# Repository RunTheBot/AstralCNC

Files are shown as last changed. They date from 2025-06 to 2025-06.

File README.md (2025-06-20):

# AstralCNC

A Replacement board for the Larken **StarCNC** controller. Built around the RPI Pico, this board is designed with safety and flexibility in mind, allowing for easy integration with external stepper drivers and digital inputs.

Powered by the Raspberry Pi Pico and GRBL-HAL.

Made to referbrish a Larken 24/24 router at my school that is over 25 years old.

# Features
- Supports up to 8 external stepper drivers (5v IO, Step/Dir)
- Supports up to 8 external digital inputs (3.3v IO)
- 5v IO can be switched to 3.3v IO
- 3.3v IO can be switched to 5v IO (for external stepper drivers)
- Built-in 12v regulator for powering all components
- Hardware level emergency stop
  - Emergency stop is not relient on software, ensuring that it works even if the software crashes as the stepper drivers put out a good ammount of EMI
- Hardware level reset button
  - Reset after an emergency stop is not relient on software, ensuring that the machine will remain stopped until it is manually reset
- 4 Analog inputs (ADC)
- All IO is PWM capable

# Images
Larken StarCNC
Schematic
PCB

# BOM

| Name | Quantity | Single Unit Price | Total Price | URL/LCSC | FALSE | Vendor (LCSC unless otheriwse indicated) |
|---|---|---|---|---|---|---|
| Electronics | | | | | FALSE | |
| 47pF | 1 | N/A | $0.29 | C105622 | FALSE | |
| 0.1uF | 1 | N/A | | | FALSE | With My other two projects |
| 22uF | 2 | N/A | $0.17 | C59461 | FALSE | |
| 4.7uF | 2 | N/A | $0.15 | C69335 | FALSE | |
| Molex_KK-254_AE-6410-02A_1x02_P2.54mm_Vertical | 1 | N/A | $0.40 | C5447965 | FALSE | |
| Molex_KK-254_AE-6410-10A_1x10_P2.54mm_Vertical | 1 | N/A | $0.39 | C30169 | FALSE | |
| PinHeader_2x04_P2.54mm_Vertical | 1 | N/A | $0.39 | C2829882 | FALSE | |
| PinHeader_1x04_P2.54mm_Vertical | 7 | N/A | $0.42 | C2935910 | FALSE | |
| Molex_KK-254_AE-6410-03A_1x03_P2.54mm_Vertical | 4 | N/A | $0.71 | C29275 | FALSE | |
| 6.8UH | 1 | N/A | $1.18 | C5296375 | FALSE | |
| BC847 | 3 | N/A | $0.46 | C57668 | FALSE | |
| 220k | 1 | N/A | $0.10 | C22961 | FALSE | |
| 41.2k | 1 | N/A | $0.10 | C2930101 | FALSE | |
| 93.1k | 1 | N/A | $0.10 | C2933266 | FALSE | |
| 22k | 1 | N/A | $0.09 | C2907015 | FALSE | |
| 10k | 6 | N/A | | | FALSE | With My other two projects |
| AP63357 | 1 | N/A | $0.52 | C2158014 | FALSE | |
| 74HC244 | 2 | N/A | $0.77 | C5623 | FALSE | |
| RP2350_Stamp | 1 | N/A | $12.05 | https://lectronz.com/products/rp2350-stamp | FALSE | |
| TXS0108EPW | 2 | N/A | $1.12 | C17206 | FALSE | |
| MOLEX 22013037 | 4 | | $0.27 | C22451182 | FALSE | |
| Molex 2759 seris | 12 | | $0.24 | C22451180 | FALSE | |
| PCB - JLC | | | $9.00 | | | |
| LCSC - Shipping and handling | | | $17.16 | | | |
| lectronz | | | $17.79 | | | |
| JLC - Shipping | | | $8.23 | | | |
| | | | | | | |
| | | | | | | |
| | | | | | | |
| | | | | | | |
| | | | | | | |
| | | | | | | |
| | | | | | | |
| | | | | CAD | | |
| | | | $72.10 | USD | | |
| | | | $72.10 | Total - USD | | |

Why is shipping so expensive? 😭

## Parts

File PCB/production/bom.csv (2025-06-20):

Designator | Footprint | Quantity | Value | LCSC Part #
C11 | 0603 | 1 | 47pF
C12 | 0805 | 1 | 0.1uF
C13, C14 | 0603 | 2 | 22uF
C15, C16 | 0603 | 2 | 4.7uF
J11 | Molex_KK-254_AE-6410-02A_1x02_P2.54mm_Vertical | 1 | Conn_01x02
J31 | Molex_KK-254_AE-6410-10A_1x10_P2.54mm_Vertical | 1 | Conn_01x10_Pin
J310 | PinHeader_2x04_P2.54mm_Vertical | 1 | Conn_02x04_Counter_Clockwise
J311, J312, J313, J32, J37, J38, J39 | PinHeader_1x04_P2.54mm_Vertical | 7 | Conn_01x04_Pin
J33, J34, J35, J36 | Molex_KK-254_AE-6410-03A_1x03_P2.54mm_Vertical | 4 | Conn_01x03_Pin
L11 | L_Chilisin_BMRA00050530 | 1 | 6.8UH
Q21, Q22, Q23 | SOT-23 | 3 | BC847
R11 | 0603 | 1 | 220k
R12 | 0603 | 1 | 41.2k
R13 | 1206 | 1 | 93.1k
R14 | 0603 | 1 | 22k
R21, R22, R23, R24, R25, R26 | 0603 | 6 | 10k
U11 | V-DFN3020-13 | 1 | AP63357
U21, U22 | TSSOP-20_4.4x6.5mm_P0.65mm | 2 | 74HC244
U31 | RP2xxx_Stamp_THT | 1 | RP2350_Stamp
U32, U33 | TSSOP-20_4.4x6.5mm_P0.65mm | 2 | TXS0108EPW

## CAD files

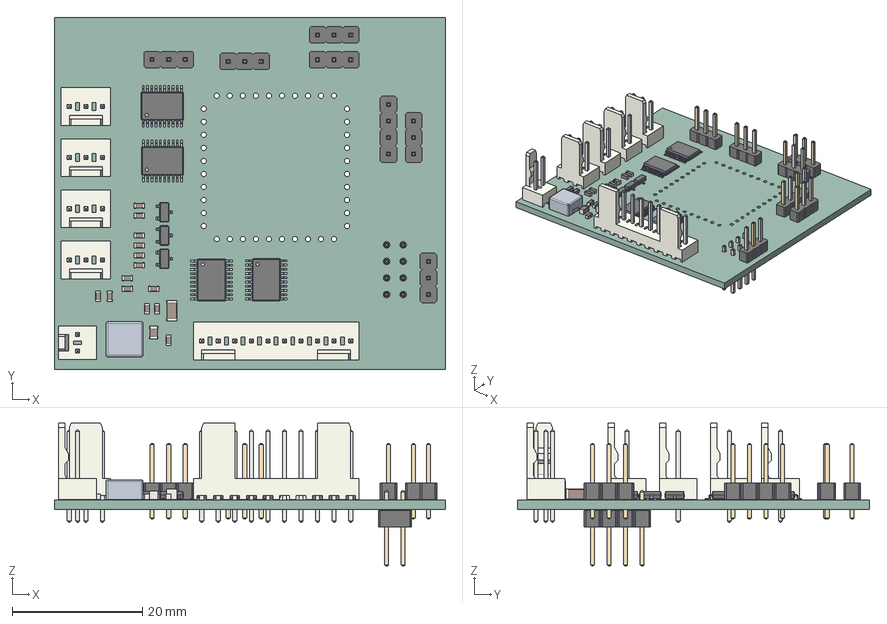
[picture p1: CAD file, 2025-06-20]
PCB/AstralCNC.step
60.0 x 54.0 x 21.9 mm
PinHeader_1x03_P2.54mm_Vertical x 6
C_1206_3216Metric
C_0603_1608Metric x 14
Molex_KK-254_AE-6410-03A_1x03_P2.54mm_Vertical x 4
C_0805_2012Metric
SOT-23 x 3
Molex_KK-254_AE-6410-02A_1x02_P2.54mm_Vertical
TSSOP-20_4.4x6.5mm_P0.65mm x 4
Molex_KK-254_AE-6410-10A_1x10_P2.54mm_Vertical
AstralCNC 1.18.1
PinHeader_1x04_P2.54mm_Vertical
PinHeader_2x04_P2.54mm_Vertical
AstralCNC_PCB

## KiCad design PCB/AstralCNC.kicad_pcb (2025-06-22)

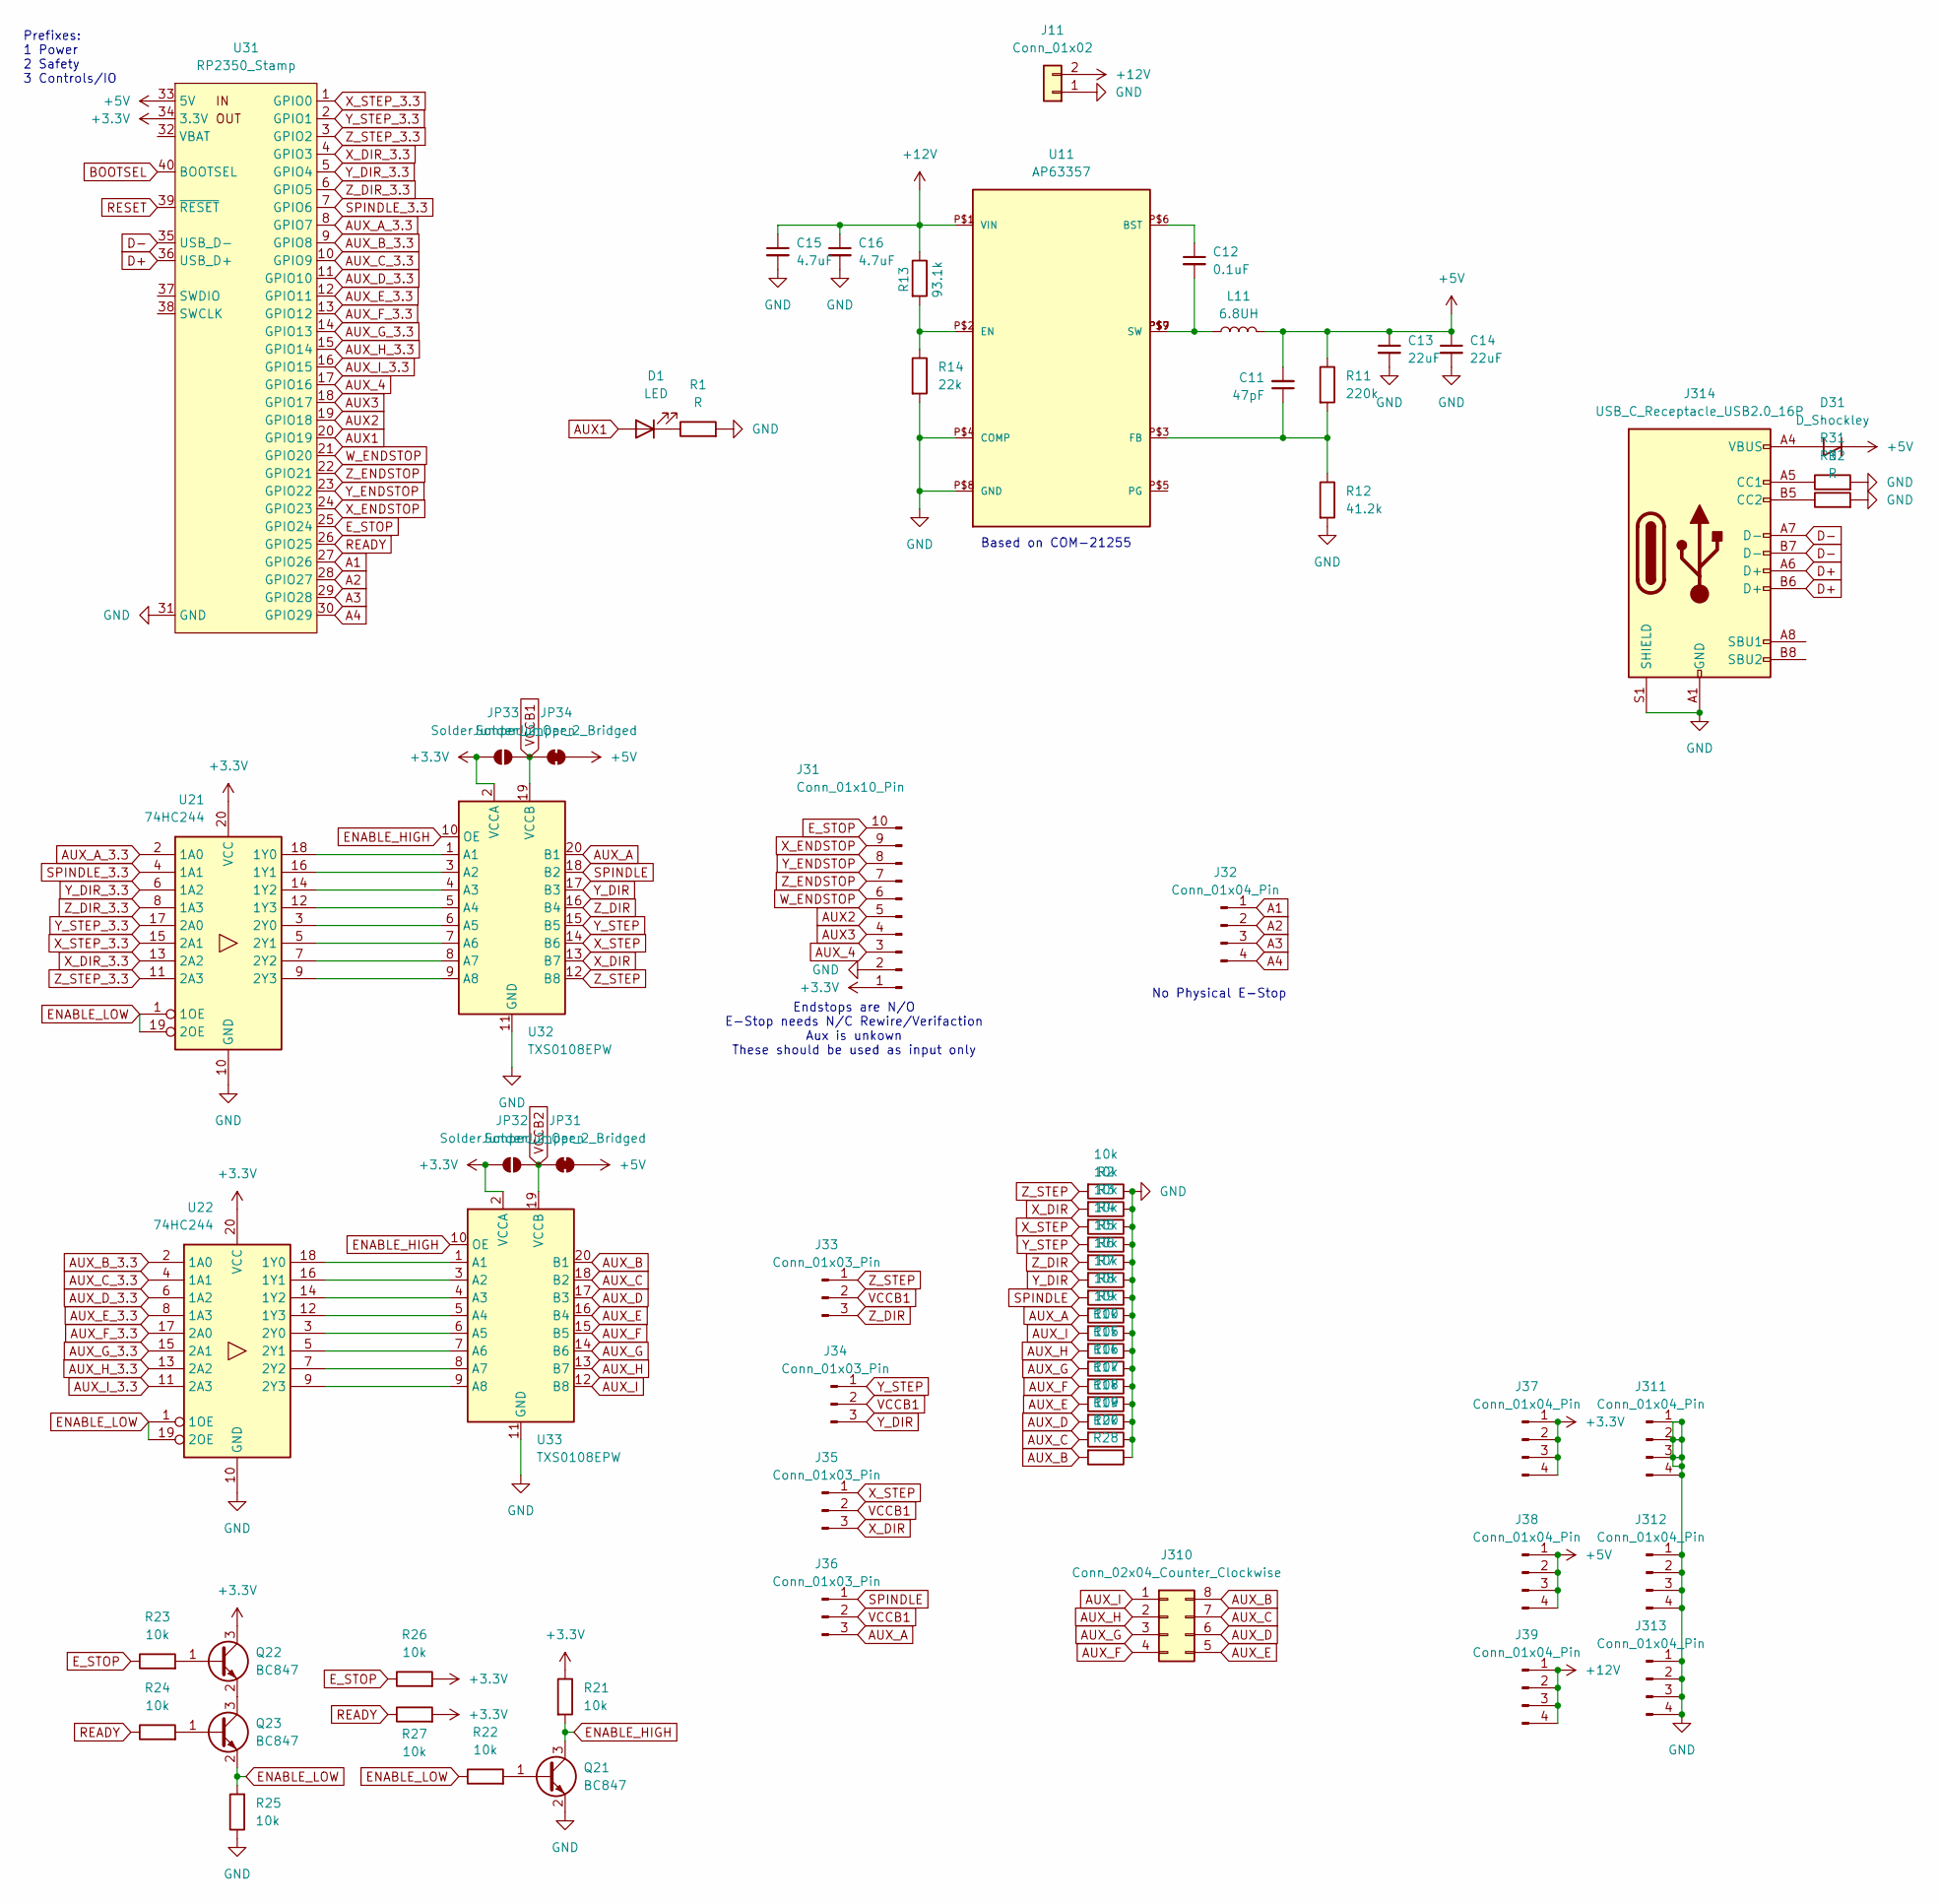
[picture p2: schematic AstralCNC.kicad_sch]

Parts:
C11: 47pF; C_0603_1608Metric_Pad1.08x0.95mm_HandSolder
C12: 0.1uF; C_0805_2012Metric_Pad1.18x1.45mm_HandSolder
C13, C14: 22uF; C_0603_1608Metric_Pad1.08x0.95mm_HandSolder
C15, C16: 4.7uF; C_0603_1608Metric_Pad1.08x0.95mm_HandSolder
D1: LED; PinHeader_1x02_P2.54mm_Vertical
D31: D_Shockley; D_SMA_Handsoldering
J11: Conn_01x02; Molex_KK-254_AE-6410-02A_1x02_P2.54mm_Vertical
J31: Conn_01x10_Pin; Molex_KK-254_AE-6410-10A_1x10_P2.54mm_Vertical
J32, J37, J38, J39, J311, J312, J313: Conn_01x04_Pin; PinHeader_1x04_P2.54mm_Vertical
J33, J34, J35, J36: Conn_01x03_Pin; Molex_KK-254_AE-6410-03A_1x03_P2.54mm_Vertical
J310: Conn_02x04_Counter_Clockwise; PinHeader_2x04_P2.54mm_Vertical
J314: USB_C_Receptacle_USB2.0_16P; USB_C_Receptacle_G-Switch_GT-USB-7010ASV
JP31, JP34: SolderJumper_2_Bridged; SolderJumper-2_P1.3mm_Bridged_RoundedPad1.0x1.5mm
JP32, JP33: SolderJumper_2_Open; SolderJumper-2_P1.3mm_Open_RoundedPad1.0x1.5mm
L11: 6.8UH; L_Chilisin_BMRA00050530
Q21, Q22, Q23: BC847; SOT-23
R1, R31, R32: R; C_0603_1608Metric_Pad1.08x0.95mm_HandSolder
R2, R3, R4, R5, R6, R7, R8, R9, R10, R15, R16, R17, R18, R19, R20, R21, R22, R23, R24, R25, R26, R27, R28: 10k; C_0603_1608Metric_Pad1.08x0.95mm_HandSolder
R11: 220k; C_0603_1608Metric_Pad1.08x0.95mm_HandSolder
R12: 41.2k; C_0603_1608Metric_Pad1.08x0.95mm_HandSolder
R13: 93.1k; C_0603_1608Metric_Pad1.08x0.95mm_HandSolder
R14: 22k; C_0603_1608Metric_Pad1.08x0.95mm_HandSolder
U11: AP63357; V-DFN3020-13
U21, U22: 74HC244; TSSOP-20_4.4x6.5mm_P0.65mm
U31: RP2350_Stamp; RP2xxx_Stamp_THT
U32, U33: TXS0108EPW; TSSOP-20_4.4x6.5mm_P0.65mm

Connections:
+3.3V: J31.1, J37.1, J37.2, J37.3, J37.4, JP32.1 (A), JP33.1 (A), Q22.3 (C), R21.1, R26.2, R27.2, U21.20 (VCC), U22.20 (VCC), U31.34 (3.3V), U32.2 (VCCA), U33.2 (VCCA)
+5V: C11.2, C13.1, C14.1, D31.1 (K), J38.1, J38.2, J38.3, J38.4, JP31.2 (B), JP34.2 (B), L11.2, R11.1, U31.33 (5V)
+12V: C15.1, C16.1, J11.2, J39.1, J39.2, J39.3, J39.4, R13.1, U11.P$1 (VIN)
A1: J32.1, U31.27 (GPIO26)
A2: J32.2, U31.28 (GPIO27)
A3: J32.3, U31.29 (GPIO28)
A4: J32.4, U31.30 (GPIO29)
AUX1: D1.2 (A), U31.20 (GPIO19)
AUX2: J31.5, U31.19 (GPIO18)
AUX3: J31.4, U31.18 (GPIO17)
AUX_4: J31.3, U31.17 (GPIO16)
AUX_A: J36.3, R9.2, U32.20 (B1)
AUX_A_3.3: U21.2 (1A0), U31.8 (GPIO7)
AUX_B: J310.8, R28.2, U33.20 (B1)
AUX_B_3.3: U22.2 (1A0), U31.9 (GPIO8)
AUX_C: J310.7, R20.2, U33.18 (B2)
AUX_C_3.3: U22.4 (1A1), U31.10 (GPIO9)
AUX_D: J310.6, R19.2, U33.17 (B3)
AUX_D_3.3: U22.6 (1A2), U31.11 (GPIO10)
AUX_E: J310.5, R18.2, U33.16 (B4)
AUX_E_3.3: U22.8 (1A3), U31.12 (GPIO11)
AUX_F: J310.4, R17.2, U33.15 (B5)
AUX_F_3.3: U22.17 (2A0), U31.13 (GPIO12)
AUX_G: J310.3, R16.2, U33.14 (B6)
AUX_G_3.3: U22.15 (2A1), U31.14 (GPIO13)
AUX_H: J310.2, R15.2, U33.13 (B7)
AUX_H_3.3: U22.13 (2A2), U31.15 (GPIO14)
AUX_I: J310.1, R10.2, U33.12 (B8)
AUX_I_3.3: U22.11 (2A3), U31.16 (GPIO15)
BOOTSEL: U31.40 (BOOTSEL)
D+: J314.A6 (D+), J314.B6 (D+), U31.36 (USB_D+)
D-: J314.A7 (D-), J314.B7 (D-), U31.35 (USB_D-)
ENABLE_HIGH: Q21.3 (C), R21.2, U32.10 (OE), U33.10 (OE)
ENABLE_LOW: Q23.2 (E), R22.1, R25.2, U21.1 (1OE), U21.19 (2OE), U22.1 (1OE), U22.19 (2OE)
E_STOP: J31.10, R23.1, R26.1, U31.25 (GPIO24)
GND: C13.2, C14.2, C15.2, C16.2, J11.1, J31.2, J311.1, J311.2, J311.3, J311.4, J312.1, J312.2, J312.3, J312.4, J313.1, J313.2, J313.3, J313.4, J314.A1 (GND), J314.A12 (GND), J314.B1 (GND), J314.B12 (GND), J314.S1 (SHIELD), Q21.2 (E), R1.2, R2.1, R3.1, R4.1, R5.1, R6.1, R7.1, R8.1, R9.1, R10.1, R12.2, R14.2, R15.1, R16.1, R17.1, R18.1, R19.1, R20.1, R25.1, R28.1, R31.2, R32.2, U11.P$4 (COMP), U11.P$8 (GND), U21.10 (GND), U22.10 (GND), U31.31 (GND), U32.11 (GND), U33.11 (GND)
unnamed: C12.2, L11.1, U11.P$7 (SW), U11.P$9 (SW)
unnamed: D1.1 (K), R1.1
unnamed: D31.2 (A), J314.A4 (VBUS), J314.A9 (VBUS), J314.B4 (VBUS), J314.B9 (VBUS)
unnamed: J314.A5 (CC1), R31.1
unnamed: J314.B5 (CC2), R32.1
unnamed: Q21.1 (B), R22.2
unnamed: Q22.1 (B), R23.2
unnamed: Q22.2 (E), Q23.3 (C)
unnamed: Q23.1 (B), R24.2
unnamed: C12.1, U11.P$6 (BST)
unnamed: R13.2, R14.1, U11.P$2 (EN)
unnamed: C11.1, R11.2, R12.1, U11.P$3 (FB)
unnamed: U21.18 (1Y0), U32.1 (A1)
unnamed: U21.16 (1Y1), U32.3 (A2)
unnamed: U21.14 (1Y2), U32.4 (A3)
unnamed: U21.12 (1Y3), U32.5 (A4)
unnamed: U21.3 (2Y0), U32.6 (A5)
unnamed: U21.5 (2Y1), U32.7 (A6)
unnamed: U21.7 (2Y2), U32.8 (A7)
unnamed: U21.9 (2Y3), U32.9 (A8)
unnamed: U22.18 (1Y0), U33.1 (A1)
unnamed: U22.16 (1Y1), U33.3 (A2)
unnamed: U22.14 (1Y2), U33.4 (A3)
unnamed: U22.12 (1Y3), U33.5 (A4)
unnamed: U22.3 (2Y0), U33.6 (A5)
unnamed: U22.5 (2Y1), U33.7 (A6)
unnamed: U22.7 (2Y2), U33.8 (A7)
unnamed: U22.9 (2Y3), U33.9 (A8)
READY: R24.1, R27.1, U31.26 (GPIO25)
RESET: U31.39 (~RESET)
SPINDLE: J36.1, R8.2, U32.18 (B2)
SPINDLE_3.3: U21.4 (1A1), U31.7 (GPIO6)
VCCB1: J33.2, J34.2, J35.2, J36.2, JP33.2 (B), JP34.1 (A), U32.19 (VCCB)
VCCB2: JP31.1 (A), JP32.2 (B), U33.19 (VCCB)
W_ENDSTOP: J31.6, U31.21 (GPIO20)
X_DIR: J35.3, R3.2, U32.13 (B7)
X_DIR_3.3: U21.13 (2A2), U31.4 (GPIO3)
X_ENDSTOP: J31.9, U31.24 (GPIO23)
X_STEP: J35.1, R4.2, U32.14 (B6)
X_STEP_3.3: U21.15 (2A1), U31.1 (GPIO0)
Y_DIR: J34.3, R7.2, U32.17 (B3)
Y_DIR_3.3: U21.6 (1A2), U31.5 (GPIO4)
Y_ENDSTOP: J31.8, U31.23 (GPIO22)
Y_STEP: J34.1, R5.2, U32.15 (B5)
Y_STEP_3.3: U21.17 (2A0), U31.2 (GPIO1)
Z_DIR: J33.3, R6.2, U32.16 (B4)
Z_DIR_3.3: U21.8 (1A3), U31.6 (GPIO5)
Z_ENDSTOP: J31.7, U31.22 (GPIO21)
Z_STEP: J33.1, R2.2, U32.12 (B8)
Z_STEP_3.3: U21.11 (2A3), U31.3 (GPIO2)

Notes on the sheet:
Prefixes: 1 Power 2 Safety 3 Controls/IO
Endstops are N/O E-Stop needs N/C Rewire/Verifaction Aux is unkown These should be used as input only
No Physical E-Stop
Based on COM-21255

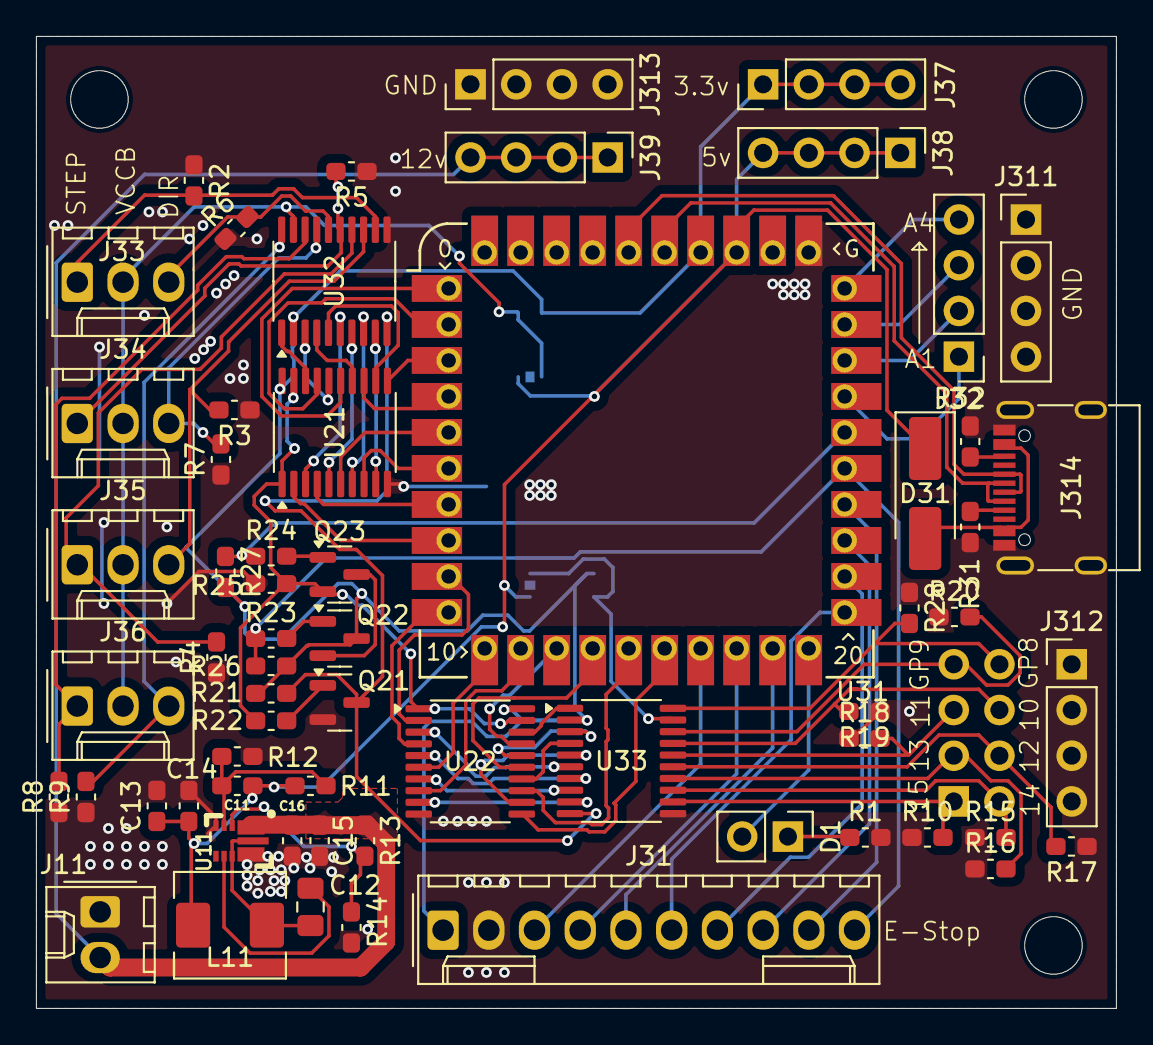
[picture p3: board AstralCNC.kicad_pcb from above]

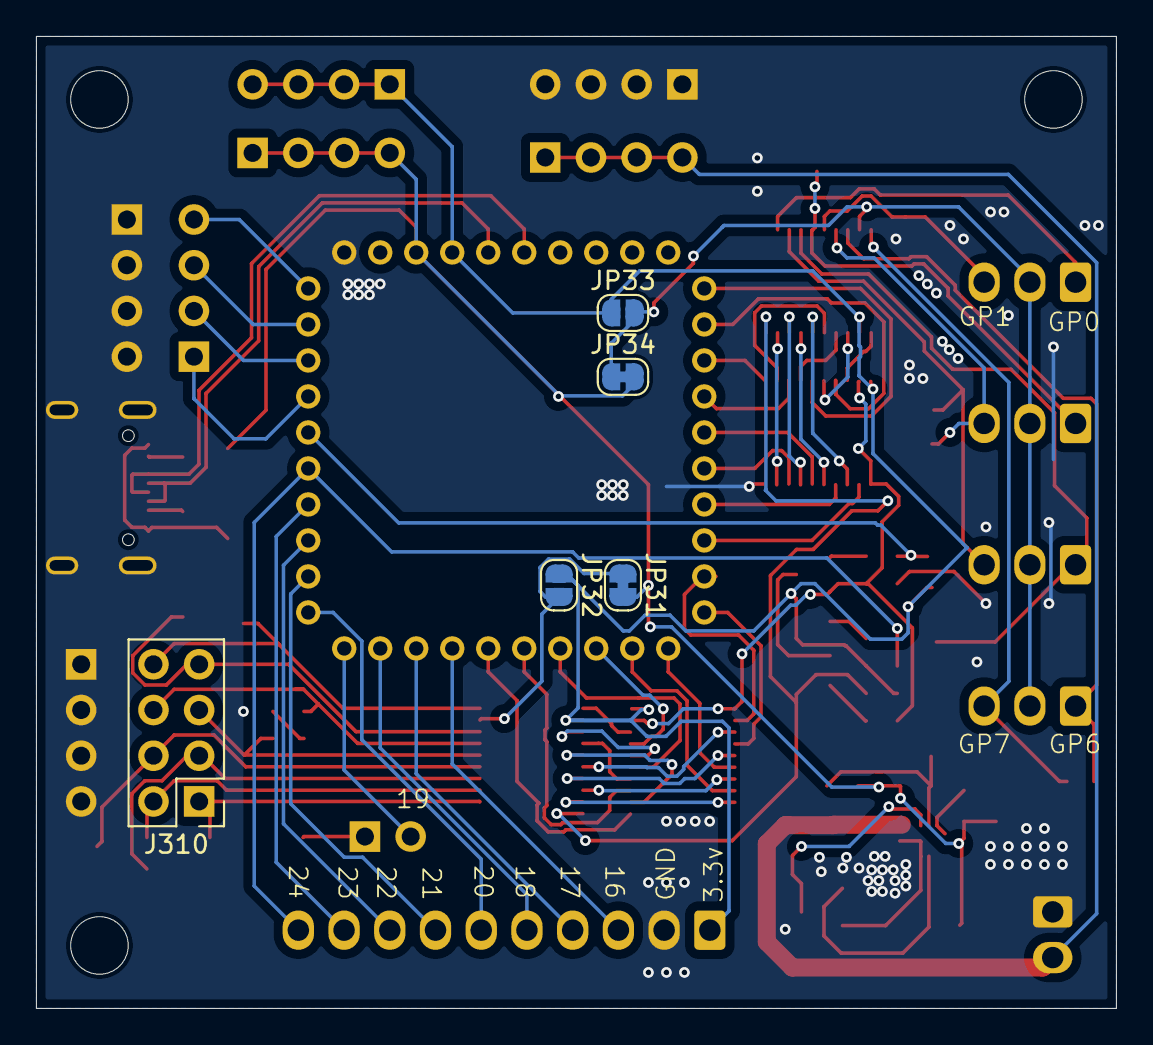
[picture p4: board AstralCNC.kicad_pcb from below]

Board: 2 copper layers, 60.0 x 54.0 mm, 67 parts (5 on the bottom side), 84 nets.

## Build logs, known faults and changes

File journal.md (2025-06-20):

---
title: "AstralCNC"
author: "RunTheBot"
description: "Replacement board for the Larken StarCNC controller, built around the RPI Pico."
created_at: "2025-06-17"
---
# Journal

Hours: 21h

# A while back, right before highway announced to June 16
Hours: 3h

When I got to this school, I've always wanted to fix the two CNCs that we have. One of them is a Larken 24/24 router, which is over 25 years old.

The controller uses a parrallel port which moder Operating systems don't support anymore, and the software that it uses is very old and doesn't work on modern computers.

I did a bunch of research and I needed to find the controller box which my teacher conviniently knew where it was. I took it home and started trying to use the parrallel port not knowing that it was not supported by modern operating systems.

After that I started looking for alternatives and documentation on how the controller works. I found (https://www.larkencnc.com/dloads/index.shtml)[https://www.larkencnc.com/dloads/index.shtml] which has a lot of documentation on the controller and how it works.

Larken StarCNC

# June 16-17

Hours: 2h

Me and my friend (Jayson) started hacking at the controller using a Pico. We started by directly connecting the Pico to the stepper drivers and using the Pico's GPIO to control them. it kind of worked. 

I soon figured out that the Pico's GPIO is 3.3v and the stepper drivers are 5v, so we made a level shifter using some mosfets and some resistors. This worked, but I unfortunately did not get pictures of it.

heres the code:
```python
import board
import digitalio
import time
import supervisor

# Pins
step_pin = digitalio.DigitalInOut(board.GP0)
step_pin.direction = digitalio.Direction.OUTPUT

dir_pin = digitalio.DigitalInOut(board.GP1)  # Change if using a different pin
dir_pin.direction = digitalio.Direction.OUTPUT

# Settings
step_delay = 0.01  # Default speed

# Functions
def step_motor(steps):
    for _ in range(steps):
        step_pin.value = True
        time.sleep(step_delay)
        step_pin.value = False
        time.sleep(step_delay)

def set_direction(direction):
    dir_pin.value = bool(direction)

def set_speed(level):
    global step_delay
    step_delay = max(0.001, min(0.1, 0.1 / level))  # Level 1–10

def print_help():
    print("Commands:")
    print("  step <n>     - Step motor n times")
    print("  dir <0|1>    - Set direction")
    print("  speed <1-10> - Set speed level")
    print("  help         - Show this help")

print("Stepper Control Ready. Type 'help'.")

# Main loop
while True:
    if supervisor.runtime.serial_bytes_available:
        try:
            line = input().strip()
            if not line:
                continue
            parts = line.split()
            cmd = parts[0].lower()

            if cmd == "step" and len(parts) == 2:
                step_motor(int(parts[1]))
                print(f"Stepped {parts[1]} times.")

            elif cmd == "dir" and len(parts) == 2:
                set_direction(int(parts[1]))
                print(f"Direction set to {parts[1]}.")

            elif cmd == "speed" and len(parts) == 2:
                set_speed(int(parts[1]))
                print(f"Speed level set to {parts[1]}.")

            elif cmd == "help":
                print_help()

            else:
                print("Unknown command. Type 'help'.")

        except Exception as e:
            print("Error:", e)
```

I then tested the spindle and it is just a simple solid state relay running off 5v, so I connected it to the Pico and it worked.

# June 17
Hours: 3h

I started by exploring software options. Here are the options I found:

FluidNC: A very good option, for ESP32 but I didn't want to use it because people (ChatGPT) did not recommend it for CNCs.
Remora: Very new and modern but small community, so I didn't want to use it.
GRBL-HAL: Best ive seen, a bit dated but very good documentation and a large community. I decided to use it.

I continued with a Pico as the docs recommended it, and I started by making a simple schematic of the board.

I also looked at linuxcnc, but it added a bit too much complexity for my use case, and I didn't want add a full computer to the CNC.

# June 17

Hours: 3h

Schematic!
Schematic

# June 18-19
hours: 6h
PCB design!

PCB

# June 19
hours: 4h

BOM and journal
https://docs.google.com/spreadsheets/d/1fKyxs4xyiDP1QXcRQpTOFPQCPsDcIa7fzhB4tR6pHxY/edit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

Side note: why does LCSC not stock Molex KK-254 connectors? ts pmo
Side note 2: Why are molex product nameing so bad? We have two manufacturer product numbers, two series names, and like no consistency.

Polish and added usb c connector because I forgot lol.

sadas

# June 20
Hours: 1h
Fixed up some silkscreen issues, added some more silkscreen text, and exposed an IO pin I forgot to expose.

Thanks to Larry Kenny (The guy who made the original controller) for making the documentation available and awnswering my questions.

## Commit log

2025-06-20 Add initial files for AstralCNC project
    - Created positions.csv for component placement data.
    - Added sym-lib-table for symbol library references.
    - Introduced lock files for PCB and schematic to manage editing sessions.
    - Added README.md with project overview, features, images, and BOM.
    - Created journal.md to document project progress and development notes.
    [AstralCNC - BOM - LCSC.csv, AstralCNC.kicad_pcb, AstralCNC.kicad_sch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]
2025-06-20 Update journal entries: Adjusted hours for June 17 and June 19, added USB-C connector details, and included an image for clarity.
    [AstralCNC.kicad_pcb]
2025-06-22 Add submodule for AstralCNC-grblHAL and update backup files
2025-06-22 Added pull downs for safety
    [AstralCNC.kicad_pcb, AstralCNC.kicad_sch]
